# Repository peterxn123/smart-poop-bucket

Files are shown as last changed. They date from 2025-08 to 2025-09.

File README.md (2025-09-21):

# smart-poop-bucket

Physical build:







Smart 3D printer poop bucket suitable for the Bambu A1. Track your poop with the web interface. Uses a Xiao ESP32-S3, HX711 and a 50kg load cell. This very handy tool makes it easier to manage your (printer) poop, by allowing you to monitor live your poop grammage for each print. As I'm sure you know, the slicer's estimate is only just that - an estimate - and so when it is important to know the total filament usage, for example when calculating the cost of a 3D print to sell, this handy tool allows you to see the exact weight of poop output by the printer per print. Uses the public HX711 micropython lib, so this project is therefore shared under an MIT license.

Why did I create this? Well, simply put, I hate the waste produced by multicolour prints. I like to minimise my waste when printing, and also when I sell my multicolour prints I need to calculate the price by including the weight of the poop and the printed objects. So, I thought it would be really handy, rather than me having to empty my poop bin and weigh it myself every time, instead have a smart poop bin where I can keep track of the poop weight of each print, without having to go through the hassle of weighing it myself. This should make selling 3D prints easier for anyone who uses the AMS lite system with their A1.

**The poop bucket itself, with the minecraft chest theme:**





**The PCB:**



**The base which houses the electronics and weigh scales - the chest goes on top of this**



**Bottom side of the base:**



**The chest and the base together:**



```

Wiring diagram:

             ┌──────────────────────────────────────────────┐
             │                 Generic ESP32-S3             │
             │                                              │
             │ GPIO16 ────────► DT (HX711)                  │
             │ GPIO17 ────────► SCK (HX711)                 │
             │ 3V3   ────────► VCC (HX711)                  │
             │ GND   ────────► GND (HX711)                  │
             └──────────────────────────────────────────────┘

             ┌──────────────────────────────────────────────┐
             │                  HX711 Module                │
             │                                              │
             │ VCC   ◄─────── 3V3 (ESP32-S3)                │
             │ GND   ◄─────── GND (ESP32-S3)                │
             │ DT    ◄─────── GPIO4 (ESP32-S3)              │
             │ SCK   ◄─────── GPIO5 (ESP32-S3)              │
             │ E+    ◄─────── Red wire (Load Cell)          │
             │ E-    ◄─────── Black wire (Load Cell)        │
             │ A-    ◄─────── White wire (Load Cell)        │
             └──────────────────────────────────────────────┘

             ┌──────────────────────────────────────────────┐
             │                50kg Load Cell                │
             │                                              │
             │ Red   ───────► E+ (HX711)                    │
             │ Black ───────► E- (HX711)                    │
             │ White ───────► A- (HX711)                    │
             └──────────────────────────────────────────────┘

```

BOM:

| Quantity | Component | Model / Description | Purchase Link | Cost (GBP) |
|---|---|---|---|---|
| 1 | Xiao ESP32-S3 | Xiao ESP32-S3 devboard | [Link to ESP32-S3](https://www.aliexpress.com/item/1005007426784408.html?spm=a2g0o.productlist.main.1.28895274bF7p0T) | £9.19 |
| 1 | HX711 Load Cell Amplifier + 50KG | HX711 24-bit ADC module bundled with 50kg load cells | [Link to HX711 Load Cell](https://www.amazon.co.uk/Weighting-Half-bridge-Amplifier-Bathroom-Arduino/dp/B07FMN1DBN/ref=sr_1_45) | £7.98 |
| 40 | Jumper Wires (male–female) | Dupont jumper wires set | [Link to Jumper Wires](https://www.amazon.co.uk/40pcs-Dupont-Female-Jumper-Connectors/dp/B013EW65H2/ref=sr_1_28) | £3.99 |
| 1 | Custom PCB | JLCPCB fabricated PCB | [JLCPCB](https://jlcpcb.com) | £1.57 ($2) |
| | | | | **£22.73** |

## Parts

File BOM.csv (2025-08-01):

Quantity | Component | Model / Description | Amazon UK Link | Notes
1 | ESP32-S3 | Generic ESP32-S3 devboard. | https://www.amazon.co.uk/ESP32-DevKitC-WROOM1-Development-Bluetooth/dp/B0CLD4QKT1 | Main MCU with Wi-Fi + USB-C
1 | HX711 Load Cell Amplifier + 50KG load cells. | HX711 24-bit ADC module bundled together with 50kg load cells. | https://www.amazon.co.uk/Weighting-Half-bridge-Amplifier-Bathroom-Arduino/dp/B07FMN1DBN | Amplifies load cell signal
40 | Jumper wires (male–female) | Dupont jumper wires set | https://www.amazon.co.uk/40pcs-Dupont-Female-Jumper-Connectors/dp/B013EW65H2 | To connect load cell and HX711 to XIAO

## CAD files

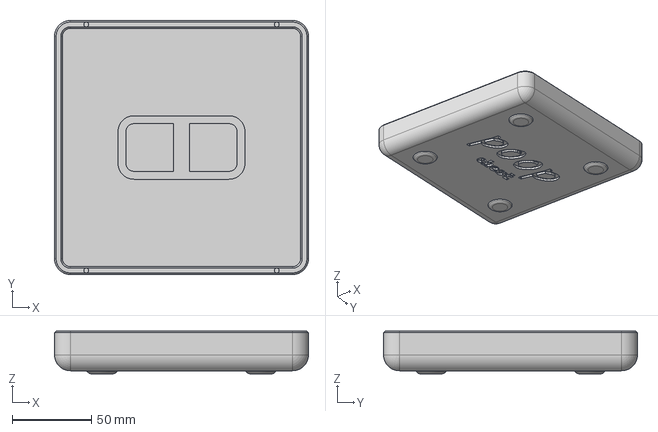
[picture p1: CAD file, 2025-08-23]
CAD/poop bucket base v10.step
160.0 x 160.0 x 27.0 mm

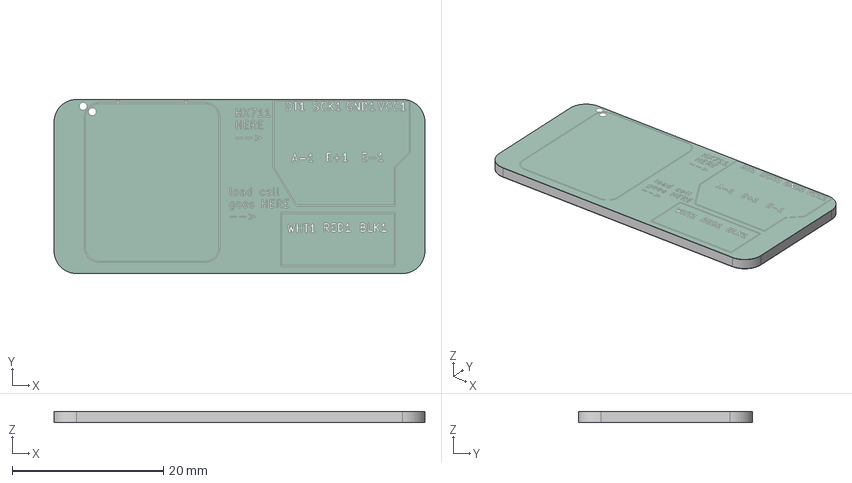
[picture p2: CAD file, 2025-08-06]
pcb/smartpoopbucket.step
49.0 x 23.0 x 1.66 mm
smartpoopbucket_silkscreen
smartpoopbucket_soldermask
smartpoopbucket_PCB

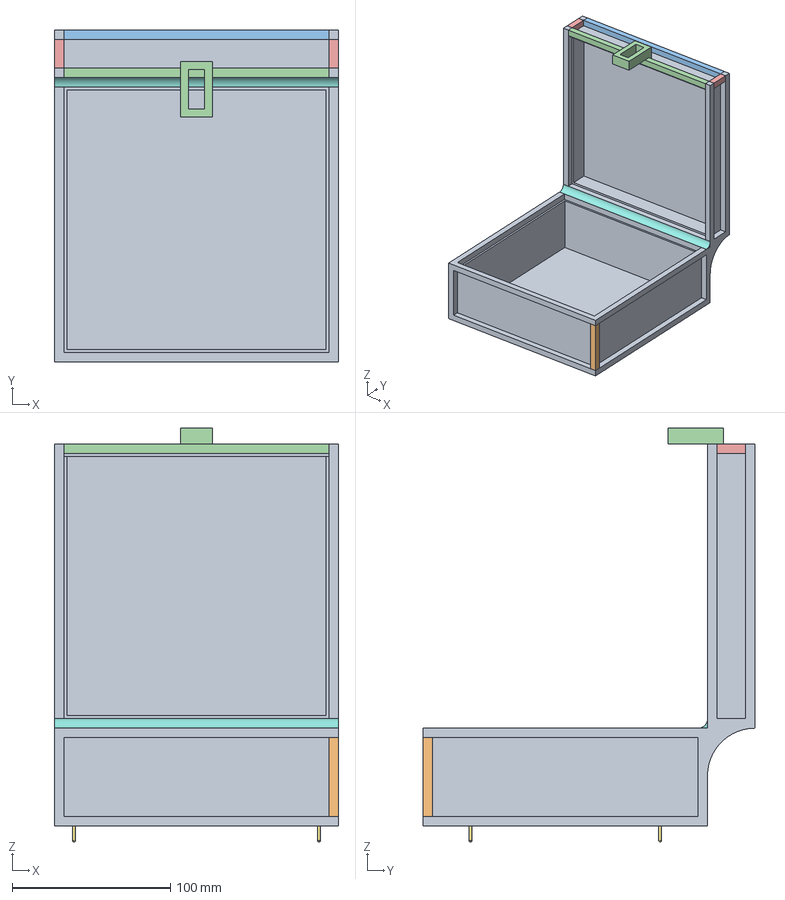
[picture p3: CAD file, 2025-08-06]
CAD/poop-bucket-chest.step
180.0 x 210.0 x 262.0 mm

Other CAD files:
CAD/SOURCE/poop-bucket-bucket.f3d

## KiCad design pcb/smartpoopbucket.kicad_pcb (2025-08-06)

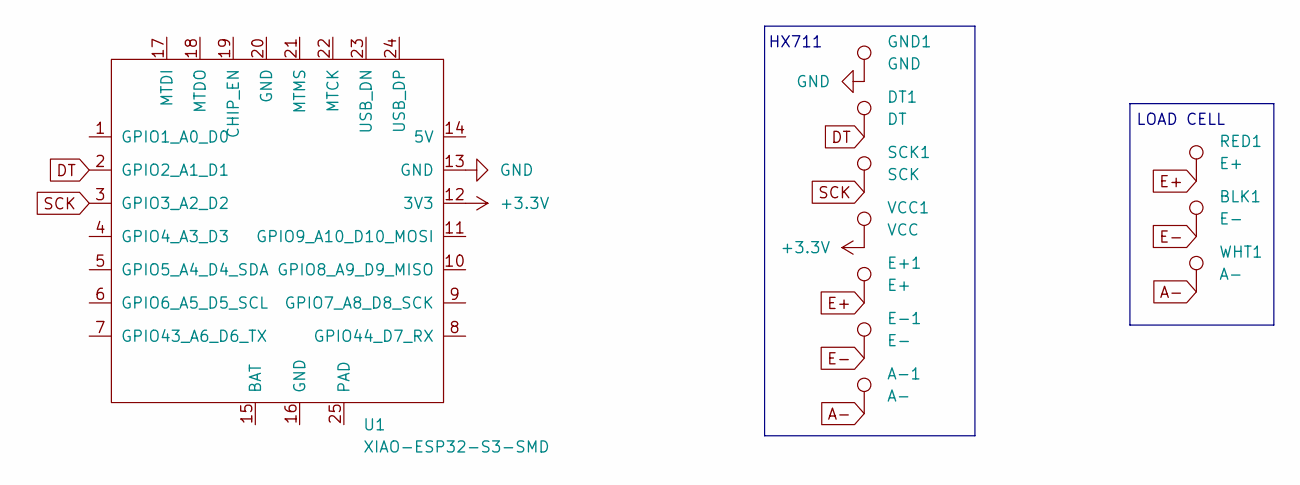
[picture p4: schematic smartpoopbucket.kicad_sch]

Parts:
A-1: A-; SolderWirePad_1x01_SMD_1x2mm
BLK1: E-; SolderWirePad_1x01_SMD_1x2mm
DT1: DT; SolderWirePad_1x01_SMD_1x2mm
E+1: E+; SolderWirePad_1x01_SMD_1x2mm
E-1: E-; SolderWirePad_1x01_SMD_1x2mm
GND1: GND; SolderWirePad_1x01_SMD_1x2mm
RED1: E+; SolderWirePad_1x01_SMD_1x2mm
SCK1: SCK; SolderWirePad_1x01_SMD_1x2mm
U1: XIAO-ESP32-S3-SMD; XIAO-ESP32S3-SMD
VCC1: VCC; SolderWirePad_1x01_SMD_1x2mm
WHT1: A-; SolderWirePad_1x01_SMD_1x2mm

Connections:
+3.3V: U1.12 (3V3), VCC1.1
A-: A-1.1, WHT1.1
DT: DT1.1, U1.2 (GPIO2_A1_D1)
E+: E+1.1, RED1.1
E-: BLK1.1, E-1.1
GND: GND1.1, U1.13 (GND)
SCK: SCK1.1, U1.3 (GPIO3_A2_D2)

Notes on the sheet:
LOAD CELL
HX711

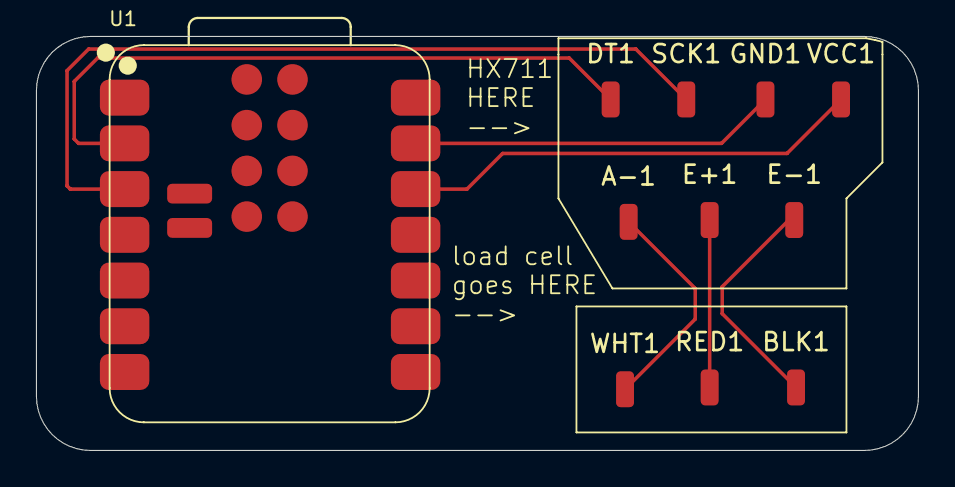
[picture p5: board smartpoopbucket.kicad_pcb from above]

Board: 2 copper layers, 49.0 x 23.0 mm, 11 parts (0 on the bottom side), 7 nets.

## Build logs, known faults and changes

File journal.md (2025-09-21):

**Smart Poop Bucket**

**Designing**

Total time spent: 12h

*July 29th - Made a start*

For my highway project, I wanted to solve a real problem in my life. So I thought about it properly. I spent a while going around my house looking and thinking about things that I could solve with a hardware project. Then it hit me. What if I could help solve the bane of my existence as someone who 3D prints a lot - the piles of poop which I have to weigh every time I finish a print, if I want to sell it?
I thought if I could create a smart bucket with built in scales which weigh the poop for me, with an easily accessible interface to see the weight, then this would be very helpful!

So, I then spent a while deciding on the hardware.

I decided I wanted a web interface for my poop bucket to make the figures easy to access. For this reason I needed a dev board which was reasonably powerful with a wifi antenna. This is how I decided on the ESP32-S3, as it is a powerful yet cheap devboard which I have heard good things about in the past.
Then, for weighing the poop, I knew I needed a load cell, as I remembered researching them when I had to replace one on the auto calibrating bed of my 3D printer. So, I researched the most common and easiest way to implement a load cell which was also ocmpact enough to fit into a poop bucket. This is how I stumbled across the bundles of the very popular Hx711, which was actually the top choice on google, and a few load cells aswell, in a conveient yet affordable bundle.

So there it was, my parts were decided and I was ready to go. I was excited for what was to come next.

*Time spent: 3h*



*July 30th - Worked on firmware*

I decided that today was the time to work on firmware. After thinking for a while, I decided that the best way to approach this was with micropython, as a library for the HX711 already existed. Also, micropython is something I am familiar with as I have used it a lot with Pi Picos in the past, so I thought it was best to go ahead with something I was familiar with. 

I knew I wanted a HTML site accessible on the local network, usable to monitor the status of the poop bucket and how much weight was in it. I decided to enlist the help of Github Copilot, and used it to help me verify the code I wrote. 
I began by researching how to use the HX711 library, imported it, and wrote some basic code for initialising it. I then added the HTML functionality, creating a simple HTML site and then hosting it. Github CoPilot helped me with the calibration part of the scales as I couldn't figure that out, and it also helped me link up the html to the PY as this was not something I had done before.

In the end, after much tinkering and consultation with both AI and a friend I created something that looked decent, and that my friend said would likely work, so I was happy with it.



*Time spent: 4h*

*July 31st - CAD and polish*

Finished my project today. I knew I had to get a quick start on the CAD as the highway deadline was coming up. I knew the best way to approach this would be to find a reference poop bucket design to use for my dimensions and to ensure that my own poop bucket is accurately sized. I found a design by Encrust3D on Makerworld called 'Slim A1 poop bucket'. I knew this was perfect as it had loads of positive reviews as fitting perfectly for the A1, and this is exactly what I wanted to use this poop bucket with my Bambu A1. 

So I imported the file into Fusion 360 and took some measurements. The length was 180mm, width 80mm and height 110mm. There was a cutout in the corner of 50x40mm, to make the bucket fit around the printer. 

I jumped into Fusion again, creating another file and started my sketch. I used similar dimensions, so that my bucked would fit just as well. I then extruded upwards, 20mm, then hollowed it out, by 16mm, leaving a 5mm gap on the edges. I then added the walls upwards to 110mm, to catch any flying poop and then added fillets, to make the look of the bucket better.
I decided to add a bit of flair to my design by adding a poop inset and the words 'Le poop' on the side.

This was just the bucket, however. I still needed to create the electronics enclosure housing the strain gauge that this bucket would sit on. I decide to make it the same dimensions as the bucket, to give it a seamless look. 

I then had to think about how to ensure that the strain guage could properly capture the buckets weight. I decided to add some holes inset into the base and matching dimples on the bucket which would slot in, to ensure the bucket stayed in place in one place, so the strain guage could stay well calibrated.

I then imported 3D models for all my electronics, placing in the HX711 and ESP32. I positioned them both and then created the cutout for the USB C ports.

Then, I extruded upwards and placed the imported strain guage down. I ensured that there was a gap under the part of the strain guage that measures weight, to ensure proper functionality. I adjusted the height of the strain guage until it was just sticking out of the case so it could touch the bucket.

I was now happy overall with the design, and I brought the two models together in Fusion and they matched perfectly. 

Today was a great learning experience in Fusion and it was a good opportunity to practice my CAD skills.



*Time spent: 5h*

*August 5th - building back from rejection*

My project got rejected today. Originally it was wihtout an option to resubmit, but I asked if I could anyway as I knew I had to have a project finished for my stipend. I don't mind the rejection though, as it is an opportunity to learn and improve on what I've built. So today I started by first deciding on what would improve my project. My reviewer, Kai, suggested if it was themed around something then it would stand out, and have a higher chance of being approved. He suggested a minecraft chest as an example, and after thinking about it for a bit I decided that this was a perfect theme, especially when I could print it multicolour with my AMS. 
So today the first thing that I improved, polished and gave it Minecraft theming is the firmware. The most important part to be polished is the part the user sees, no? This file, which would be hosted by the ESP - index.html - was previously incredibly bland and I'm sure this was a factor in my rejection. So, while keeping the same fundamental features, I completely redid the styling on the site by moving sections around and completely redoing the CSS. I also added clear indicators of when things weren't loading right and a refresh button if needed. The underlying scripts which connected with the ESP remained the same, while the interface the user uses was completely revamped and properly fit in to the Minecraft chest theme. I spent plenty of time on this, which I was happy to do as the end result was something very clean and polished, in my opinion.



*Time spent: 3 hours*

*August 6th - CAD and PCB grind*

I started today by reviewing my CAD. I jumped into Fusion, moved the window to one half of my screen then put a reference image of a minecraft chest on the other half. I started first by creating a sketch of a square of the same width as my old bucket, but with the depth now the same as the width to create the cube structure minecraft blocks have. I then extruded upwards, creating the bottom half of my open chest with the minecraft design already coming together.
Then I created the top half, sticking with the same width and height but a smaller depth obviously (it was vertical). At this point, the top half was just floating in mid-air behind the bottom half - obviously this would not be printable.
I only realised my mistake when Kai told me to double check everything is printable - obviously it wasn't. I fixed this by connecting them with a sketch of an arc which I then extruded creating a curve that connected the halves. 
But this design was only the bucket so far. I then designed the base which housed the electronics. I wanted it to be nearly invisible so the minecraft chest bin could take center stage - so I made its dimensions 15mm smaller than the chest's so it could hide underneath. I extruded it upwards 25mm, rounded out the corners to polish the design, and imported all the electronics parts CAD models. I used these models to create a cutout for the USB-C port on the ESP and to ensure the platform I extruded for the load cell to sit on had the right dimensions. I exported these CAD files, and added them to the repo. I was happy with my work. 



After talking to my reviewer, Kai, again, he said that the only way he could give me 4 points for my highway project, which is what I need to get my travel stipend, is if I created a PCB for it. So this is exactly what I did. I decided that the best way to go about this would be to have the MCU SMD mounted onto the PCB, then it would have traces running off it to the sides of the PCB where there would be labelled pads which i would solder wires to, to connect the separate HX711 board and load cell to the PCB.
I first created the schematic, trying to keep it as clean as possible by separating each electronic componenet and using global labels to show their connections. I used 'testpoints' for the HX711 and load cell connections so I could have one for each connection needed to these, and then each of these could be assigned the footprint of a pad which could be easily placed on the PCB.
I then moved from the schematic editor to the PCB editor, where I first placed down the MCU then arranged the pads so tracing between them would be and look as clean as possible. I then routed my traces, keeping them neat and organised, to keep up an overall very polished appearance of the PCB. It was really helpful to have KiCAD showing me, before I routed, which components connected together as this made it easy to arrange the pads properly for the best tracing. I added an outline of the board, using arcs for round corners and lines to join them together. I then added some silkscreen, outlining where the pads for each component are on the front and then a secret message on the back. Overall this PCB design process was very enjoyable and I was very happy with the finished product.



*Time spent: 6 hours*

**Physical Build**

*August 9th - Got the grant and ordered the parts so I can build it on holiday*

Today, quite a few days after Kai approved my revised project, I received an email from Jonathan letting me know I would be receiving a grant in my email in a short while and - lo and behold - a couple minutes later I got an email from HCB giving me the details of my grant! But there was a problem... Tomorrow I am going on holiday to Turkey and the time that I received the grant meant that I wouldnt be able to order parts to my house and get them in time... So the only way to get my parts before the deadline is to order them to the resort and put my trust in the courier survices of Turkey. I've ordered them off Amazon - let's just wait and hope.



*August 14th - It's the deadline... and I still haven't got my parts...*

Uh oh! Yeah, no parts. Seems like the courier service the seller used here in Turkey, named 'kolay gelsin' which translates, according to google at least, to 'good luck' is actually not as lucky as their name would say they are. I ordered my parts on the 9th, and they were meant to arrive on the 12th, but they still haven't arrived. I have contacted Amazon and they said they will investigate and they can see there is a delay with the courier company, but as I am writing this it is 10pm on the 14th so I have an inkling I won't get my parts in time for the deadline today. This was super dissapointing, but I have asked Acon from Hack Club if I could get an extension and they, being the kindest person ever, have said I can have an extension until early next week. I should be home by then so I can get the parts delivered using UK amazon which I know I can rely on. For now, I've re-ordered the parts and they should be there when I get home.



*August 19th - I'm home and hacking away*

Got back from my holiday today, and opened the front door at about 2am today to see two amazon parcels on the floor which had been posted through the letter box. These are the parts! First thing I did was sleep, because well, that's important and travelling's exhausting. Then I cracked open the parts and took a look at the loot. 4x Load Cells, 1x HX711 sensor, a pack of 40 jumper wires which I'll use to connect the components, and an ESP32-S3 board. 

After cracking open the parts, I started by taking a look at the wiring diagram of the ESP32 which was on a QR code included in the box. I did this because I knew it would help if i got all the needed wires soldered to where they need to be on the ESP, then attached the components to these wires so there'd be no mixing up where they need to connect to the microcontroller. From earlier work researching the HX711, I know I need 2 standard GPIO pins to connect to DT and SCK, and the 3V3 and GND connections. From looking at the HX711 lib docs, admittedly with some help from AI, I know that the data lines can be handled by any free, non hardware reserved GPIO pin.

So I soldered wires to GPIO16 and GPIO17 for DT and SCK, then 3V3 and GND. I made sure to use different coloured wires for each connection so I wouldn't mix them up later. I used purple for VCC, black for GND, white for DT and grey for SCK.

I'm pretty new to soldering, so I'm embarassed to say that this took me quite a while, and before I knew it the day was up. 




*Time spent: 2 and a half hours*

*August 20th - More soldering with the HX711*

Today I continued wiring the bits together. I started by taking out one load cell and the HX711 out of their packaging. I needed to solder the load cell to the HX711 so the HX711 can translate the input from the load into something the ESP can understand. This is obviously because the load cell is analogue, so you can't just wire it directly to the ESP. The load cell has 3 wires - black, white and red. I wasn't entirely sure which wire went to which pad on the HX711, especially considering there is 3 wires and 6 pads. So I asked ChatGPT to look at the docs of the HX711 and the load cell which I purchased and tell me. It told me that the black cable goes to E-, red to E+, and white to A-. So I spent some time soldering this in, which was admittedly annoying and I burned myself because the load cell wires are very thin and heated up a lot, but I managed to get a strong connection in the end. 



*Time spent: 2 hours*

*August 21st - Finishing the soldering and moving onto the software...*

Today I started with finishing my soldering. This entailed the should be easy, but still took me more than an hour task of soldering the other ends of the  5 wires I previously soldered to the ESP, to the pads on the right side of the HX711. These pads are labelled GND, DT, SCK and VCC. GND and VCC are obvious - I soldered GND to the black wire I connected to the GND pin of my ESP, and soldered the VCC pad to the purple wire I previously connected to the 3V3 pad of my ESP. For the other 2 - DT and SCK - these are the data lines which send out the data from the load cell. These can be connected to any GPIO pin and so I just soldered DT to the white wire I had previously connected to GPIO 16 and SCK to the grey wire I had previously soldered to GPIO 17. By doing this, my soldering was finished.

So, it was time to do software after finishing the soldering. I purchased a very generic ESP32 from Amazon, so I had to figure out how to first connect it to my PC, then how to download micropython on it. To be honest, this was my first ever time using an ESP but I had heard great things about them so I was happy to dive right in. To program the ESP with micropython I followed the official guide online (https://micropython.org/download/ESP32_GENERIC_S3/), used esptool to flash it and this went smoothly! It showed up as a micropython device in my computer and I checked using Thonny just as a basic check to see if I could program some basic code on it and it worked! So I was happy that my PC was connected to the ESP and that it was programmed with Micropython, ready for uploading my firmware.

I started by uploading the python I had written before actually receiving the parts. I used thonny for this - partly because its very simple for interfacing with micropythond devices and also because I'm used to it from projects I used to do with my pico. Before uploading it, I just modified the DT and SCK pins listed in the code to 16 and 17, to match what was actually connected. I also added in my network SSID and password so the ESP could connect to my network. I uploaded the code to the ESP, then accessed the web interface... and it didn't work... Oh well, I expected this, considering I wrote the code without having the parts yet. I will try and take a look at this tomorrow.

One thing I did notice though, even without taring or anything, was that by just printing the raw data I was receiving from the HX711... there was no difference between the data I was getting when there was a weight on the load cells or not. So I figured there must be an issue. I googled it, and did a bit of consulting with chatGPT and checking of the amazon page where I bought my load cells from, and realised that with the 3 wire type of load cell that I have, to actually get a proper reading you need two of them wired to the HX711 so that it can compare their values and figure out the load placed on them. It's actually the more expensive 4 wire type of load cell that you only need one of. This is no problem though as I can fix it, and I'm especially glad I caught it early. I hopped into fusion very quickly and did a quick modification of my design so that rather than one raised platform in the middle for one load cell there is now two next to each other. Sent this print off to the printer, and it should be done by tomorrow. I also needed to solder the second load cell on. Looking at the HX711 documents I found online, to connect 2 3 wire load cells you have one of them connected as I already have connected, and then the second one goes on with red and black going to the same A+ and A- as the other load cell - they share these connections. Then for the white wire, the second one went to A+ as my first one was on A-. 



*Time spent: 4 hours*

*August 22nd - Putting the bits together, working on the software*

I woke up this morning to a nicely finished, clean print of the new base. I took it upstairs and test fitted the two laod cells and they fit perfectly. I also test fit the chest shape top, and it also fit perfetly with its pins alligning well and it touching the pads of the load cells perfectly. So, I decided that it was time to put the parts together and have it ready for some proper software work. I started by gluing the load cells into their respective positions on the base. I then placed the ESP and HX711 into the case aswell, moved the internal wires around a bit until they fit properly, plugged a usb c cable into the ESP and ran it through the channel I left in the base so I could easily plug it into my computer and then placed the chest bucket part on top. Overall, a clean looking build.

After plugging the ESP into my computer, I fired up Thonny and opened my main.py file to get some work done and get it functioning properly. First thing I knew I would need is a zero function - just to set the value of the scale to zero just how you tare a kitchen scale before you weigh anything on it. This was easy to implement using the 'set offset' function already available within the HX711 library I used. This was easy to find after persuing the docs for a short while. When the /tare function is called on the web server, it takes an average of 15 readings of the raw input from the HX711 then uses the 'set_offset' function to set the current reading as the offset, to offset it back to zero. Second fundamental thing I knew I would need to do to make my scale, and any scale for that matter, to get some proper weight reading in grams out of the analoge signal that the HX711 outputs, was to set up a calibration function. This essentially means placing a known weight onto the scale, like a bottle of water weighing 500g, then telling the computer what it weighs and it calculates the ratio between the input it has and grams, to figure out how many raw input units = 1 gram and then it uses this to display every reading after that with the correct weight in grams. I first added /calibrate as an endpoint, just like all the other endpoints I added before but also added an argument to it - so /calibrate?w=500 means you are saying the weight you have on the scale is 500g. It then does a reading of the raw value like before, by taking it 15 times and taking the average. It then figures out the difference between the current raw value and the currently set offset, to get the actual raw value of our calibration weight, in this case 500g. It then divides the difference by the known weight to get the ratio - this is raw units per gram. It then stores it in calib.json so it persists even after unpluging and replugging the ESP. It then sends a response so you can use it from the web interface and it knows the calibration has been stored successfully. I'm really proud of myself for creating these endpoints myself, with minimal help from AI.

Checking it myself in thonny, by sort of having it in a 'debug mode' of sorts by just printing the value of the raw value and gram value and the offset variables ever few seconds, I can see that the tare endpoint is correctly storing an offset, and after placing a 500g bottle of water on the scales in the chest and manually calling the calibration endpoint I can see this is working too. I then placed another known weight in the chest after calibrating and the gram value is actually surprisingly accurate, so I'm happy the calibration and taring are doing their jobs properly. Excited to finish this tomorrow.



*Time spent: 5 hours*

*August 23rd - finishing it off and submitting*

Okay, sure it works right now if you manually call every endpoint and observe the readings yourself in the thonny console, but is this really how anyone wants to use it? Certainly not me. I need to get the web interface working. My problem right now is that I can't get it to ever show up when trying to get the micropyton to host it from its own internal memory. It keeps saying it doesn't exist, even though I have definitely uploaded the index.html file to the ESP's root multiple times though. Oh well though, this is only a minor hiccup, as if the endpoints work when manually calling them using the ESP's IP on my browser, and all thats happening when the web interface communicates with the ESP is its calling localhost, then surely I can just run the HTML on my PC locally, and just replace localhost with the ESP's IP? It was a really easy fix to make, and for ease of use I changed every reference to localhost to a single variable which can be changed if the IP of your ESP ever changes, or it's just really handy for first time use when configuring the web portal with the ESP's IP - instead of typing it multiple times you only have to type it once. So, after doing all this and changing the variable value to the IP of my ESP it... works! Yay! Well, almost. Previously I had only programmed in the start and stop functions into the web portal and sure, these do communicate with the endpoints properly and update the values appropriately in the table below, but they are also useless unless you can tare and calibrate the scale using the web portal aswell, because an untared and uncalibrated scale is not useful for weighing, well, anything. So I needed to add the tare and calibrate features to the web portal. First I started with the tare, because this was extremely easy. I just copied the 'stop' button over, changed its colour and then instead of making it call the '/stop' endpoint I made it call the '/tare' endpoint. Easy, right? Then, I moved onto the calibrate function which was a tougher nut to crack but still not very hard. Started by copying over the tare button, changing its colour again, changing the text within it to calibrate instead of tare. Then, I modified the JS function for the onclick of this button so that instead of immediately calling the endpoint it first makes this HTML element visible which is normally invisible then here you can type in the weight of the known weight you have put on the scales, THEN it sends this off to the ESP endpoint, and whatever weight you have put into the input box is put into the final API call, so it ends up being /calibrate?w=whateveryoutyped. And.. thats a wrap! The calibrate and tare functions work, which i tested by making the ESP print when it received an API call, and indeed it did after double checking in the console! Everything stores nicely on the table and you can see the delta of the weight of each print between pressing start and stop and even persists after a reboot! Really handy for printer poop measuring.

It works! Am I surprised?... Very! But yeah, it works and its pretty accurate wehn comparing the readings it picks up compared to my kitchen scales (i think anyway, because my kitchen scales only go down to 1g increments, rather than 0.1 of a gram). Last thing I did was takes some pictures, a demo video and submitted it to the highway demo form.

It's been a good ride, and a good build!

If you've made it to the end, thanks! You're a really cool person. :D



*Time spent: 4 hours*

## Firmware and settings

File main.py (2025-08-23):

import network
import socket
import time
import machine
import json
import os
from machine import Pin
from hx711 import HX711      # robert-hh hx711_gpio variant saved as hx711.py

PIN_DOUT = 16
PIN_SCK  = 17

pin_dout = Pin(PIN_DOUT, Pin.IN, pull=Pin.PULL_DOWN)
pin_sck  = Pin(PIN_SCK, Pin.OUT)

hx = HX711(pin_sck, pin_dout)

print(">>> main.py is running!")

CALFILE = "calib.json"

def load_calibration():
    if CALFILE in os.listdir():
        try:
            with open(CALFILE, "r") as f:
                cal = json.load(f)
            if "offset" in cal:
                try:
                    hx.set_offset(int(cal["offset"]))
                except Exception:
                    pass
            if "scale" in cal:
                try:
                    hx.set_scale(float(cal["scale"]))
                except Exception:
                    pass
            return cal
        except Exception:
            return None
    return None

def save_calibration(offset=None, scale=None):
    cal = {}
    if CALFILE in os.listdir():
        try:
            with open(CALFILE, "r") as f:
                cal = json.load(f)
        except Exception:
            cal = {}
    if offset is not None:
        cal["offset"] = int(offset)
    if scale is not None:
        cal["scale"] = float(scale)
    with open(CALFILE, "w") as f:
        json.dump(cal, f)

load_calibration()

SSID = 'VM9482679'
PASSWORD = 'oombSohukdcPek3i'

def connect_wifi():
    wlan = network.WLAN(network.STA_IF)
    wlan.active(True)
    if not wlan.isconnected():
        wlan.connect(SSID, PASSWORD)
        print("Connecting to WiFi...")
        while not wlan.isconnected():
            time.sleep(1)
    print('Connected to WiFi:', wlan.ifconfig())

HFILE = "poop_log.json"
def load_history():
    try:
        with open(HFILE, "r") as f:
            return json.load(f)
    except:
        return []

def save_history(history):
    with open(HFILE, "w") as f:
        json.dump(history, f)

history = load_history()
current_start_weight = None

def safe_raw_read(avg=5):
    try:
        return hx.read_average(avg)
    except Exception:
        return hx.read()

def safe_units_read(avg=5):
    try:
        return hx.get_units()
    except Exception:
        return safe_raw_read(avg)

def send_headers(cl, content_type="text/html"):
    cl.send('HTTP/1.0 200 OK\nAccess-Control-Allow-Origin: *\nContent-Type: {}\n\n'.format(content_type))

def start_server():
    addr = socket.getaddrinfo('0.0.0.0', 80)[0][-1]
    s = socket.socket()
    s.bind(addr)
    s.listen(1)
    print('Listening on', addr)

    while True:
        cl, addr = s.accept()
        request = cl.recv(2048).decode()
        if 'favicon' in request:
            cl.close()
            continue

        path = "/"
        try:
            first_line = request.split("\n")[0]
            parts = first_line.split(" ")
            if len(parts) >= 2:
                path = parts[1]
        except:
            pass

        response = ""
        if path.startswith("/start"):
            global current_start_weight
            current_start_weight = safe_units_read()
            response = "Started: {}".format(current_start_weight)
            send_headers(cl)
            cl.send(response)
            cl.close()
        elif path.startswith("/end"):
            end_weight = safe_units_read()
            delta = None
            if current_start_weight is not None:
                try:
                    delta = end_weight - current_start_weight
                except Exception:
                    delta = 0
            session = {
                "delta": delta,
                "start": current_start_weight,
                "end": end_weight,
                "timestamp": time.time(),
            }
            history.append(session)
            save_history(history)
            current_start_weight = None
            response = "Ended: {}".format(session)
            send_headers(cl)
            cl.send(response)
            cl.close()
        elif path.startswith("/clear"):
            history.clear()
            save_history(history)
            response = "Cleared"
            send_headers(cl)
            cl.send(response)
            cl.close()
        elif path.startswith("/data"):
            send_headers(cl, content_type="application/json")
            cl.send(json.dumps(history))
            cl.close()
        elif path.startswith("/tare"):
            time.sleep(0.1)
            offset = safe_raw_read(avg=15)
            try:
                hx.set_offset(int(offset))
            except AttributeError:
                try:
                    hx.tare()
                    offset = hx.read_average(15)
                except Exception:
                    pass
            save_calibration(offset=int(offset))
            response = "Tared (offset saved): {}".format(int(offset))
            send_headers(cl)
            cl.send(response)
            cl.close()
        elif path.startswith("/calibrate"):
            try:
                q = path.split("?",1)[1]
                params = {}
                for kv in q.split("&"):
                    if "=" in kv:
                        k,v = kv.split("=",1)
                        params[k]=v
                if "w" in params:
                    known_weight = float(params["w"])
                    raw = safe_raw_read(avg=15)
                    try:
                        off = None
                        val = hx.get_value()
                        diff = val
                    except Exception:
                        cal = None
                        try:
                            with open(CALFILE, "r") as f:
                                cal = json.load(f)
                            off = int(cal.get("offset", 0)) if cal else 0
                        except:
                            off = 0
                        diff = raw - off
                    if diff == 0:
                        response = "Error: difference is zero; ensure weight is on scale and offset is set (use /tare first)."
                    else:
                        scale = diff / known_weight
                        try:
                            hx.set_scale(scale)
                        except Exception:
                            pass
                        save_calibration(scale=scale)
                        response = "Calibrated: scale={} (raw/gram)".format(scale)
                else:
                    response = "Provide weight via ?w=GRAMS"
            except Exception as e:
                response = "Calibration error: {}".format(e)
            send_headers(cl)
            cl.send(response)
            cl.close()
        else:
            response = "<html><body><h1>HX711 ESP32</h1><p>Endpoints: /start /end /tare /calibrate?w=GRAMS /data /clear</p></body></html>"
            send_headers(cl)
            cl.send(response)
            cl.close()

import _thread

def print_loop():
    while True:
        try:
            val = safe_raw_read(avg=5)
            print("Raw:", val)
        except Exception as e:
            print("HX711 read error:", e)
        time.sleep(0.2)

_thread.start_new_thread(print_loop, ())

connect_wifi()
start_server()

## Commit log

2025-08-01 add BOM
    [BOM.csv]
2025-08-01 add CAD
2025-08-06 Add PCB files
    [smartpoopbucket-B_Cu.gbr, smartpoopbucket-B_Mask.gbr, smartpoopbucket-B_Paste.gbr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]
2025-08-06 Replaced old CAD with new upgraded CAD of the chest.
    [poop-bucket-bucket.f3d, poop-bucket-chest.step, smartpoopbucket.step]
2025-08-23 Updated CAD and firmware
    [poop bucket base v10.step, smartpoopbucket.kicad_pcb]
